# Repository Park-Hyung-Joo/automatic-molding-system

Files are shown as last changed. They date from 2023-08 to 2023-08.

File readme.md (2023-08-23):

--------------------------------------------
# Plastic Injection Molding Control System

## Abstract

This work was developed by the startup 'The Fourth Space', where senior Kim Seong-jun from the 17th generation of Barami is affiliated, as an outsourcing project for Barami's plastic injection molding machine control system.

The system is mainly divided into a heating bed (heater) that melts the plastic, a temperature sensor, and a solenoid valve that applies pressure to the melted plastic. Both the heater and the valve operate on 220VAC alternating current.

To control the 220VAC AC heater, a triac, a bidirectional switching device, was used. To control multiple triacs, each control signal is input to a 3-state buffer using a shift resistor, and the control signal is generated at the appropriate timing through a zero-detection circuit to turn the buffer on/off. This method allows for controlling the power of the AC heater. Additionally, the temperature of the AC heater is measured using a K-type temperature sensor, and by comparing it with the target temperature, the AC heater can be controlled within a range of 10 degrees of error through ON/OFF control. The solenoid valve also operates on 220VAC, so it is controlled in the same way using a triac.

--------------------------------------------------

## 220VAC Heater Control

### Triac
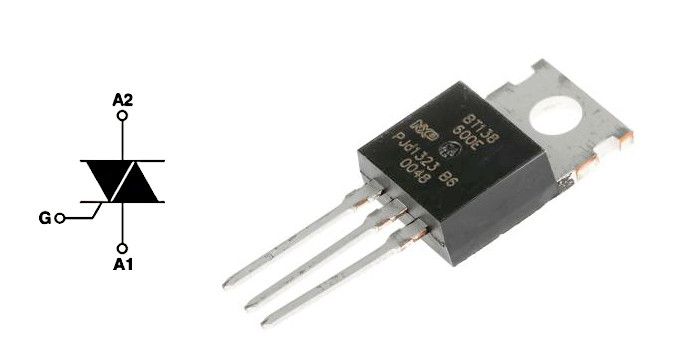
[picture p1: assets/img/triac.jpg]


A triac is a bidirectional switching device for high voltage and high current. When a pulse signal is given to the Gate, it shorts between A1 and A2 as long as the voltage value is above a certain level, and it disconnects again when the voltage drops below a threshold. The direction doesn't matter. In other words, by providing a pulse when the instantaneous voltage of the AC is 0, AC current can flow through the triac. This can be used to control the current flowing to the heater and valve.

## Triac control system

### Optocoupler Circuit

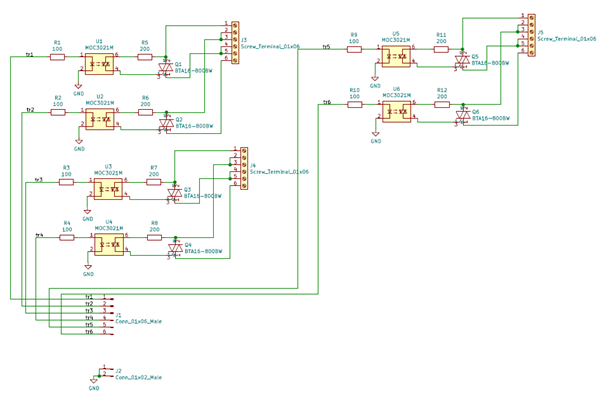
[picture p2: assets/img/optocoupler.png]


When pulses are provided to tr1~tr6 at the appropriate timing, AC current flows to the heaters connected to J3, J4, and J5. When the pulse supply is stopped, the current is cut off from the moment the AC instantaneous voltage becomes 0. The MOC3021(U1U6) device is an optocoupler, which separates the high current, high voltage AC circuit from the low voltage, low current DC circuit.

### Pulse Generator
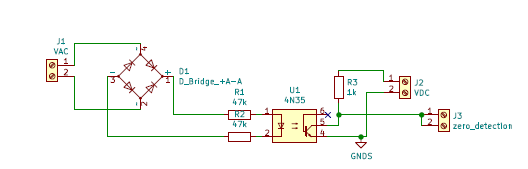
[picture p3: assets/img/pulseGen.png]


The circuit that generates the pulse produces a pulse at J3 the moment the AC voltage becomes 0. The detailed principle is as follows:

220VAC is rectified through bridge diodes and, through a resistor, provides the Photocoupler 4N35 with a rectified signal that has the same phase as 220VAC but at a lower voltage. When voltage is applied to the primary side of the 4N35, the secondary side's bjt operates, making the zero detection signal become 0. When the primary side voltage is 0, the bjt does not operate, and the zero detection voltage becomes VDC. Therefore, a pulse is generated the moment the voltage of 220VAC becomes 0.

This pulse is input into the 3-state buffer circuit.

### Tri-state Buffers
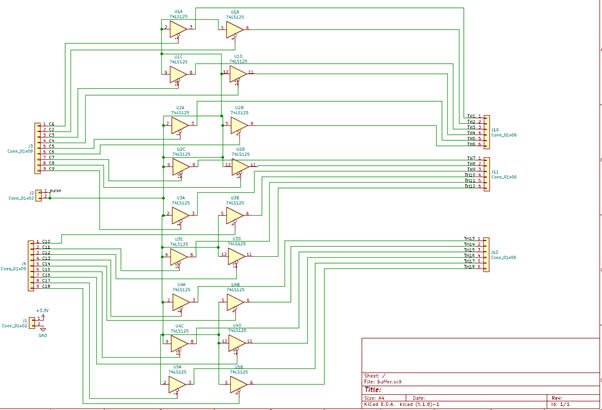
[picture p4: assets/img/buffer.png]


The tri-state buffer (buffer hereafter) circuit is divided into pulseIn, signal input, and pulseOut. When 0 is input to the signal input, the buffer passes the pulse, and when 1 is input, the pulse is blocked in the buffer. PulseOut is connected to tr1~tr6 of the above optocoupler circuit (there are a total of 3 optocoupler circuit boards). The triac is controlled by determining the signal value given to the buffer from the Arduino.

### Shift Registers
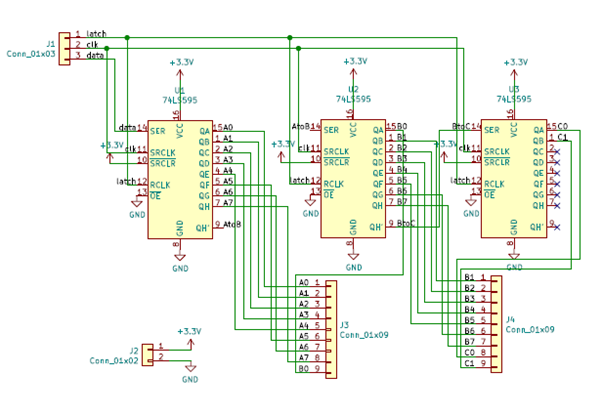
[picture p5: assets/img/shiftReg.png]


Directly inputting signals from the Arduino is unstable due to reasons like the insufficient number of Arduino pins and unstable signal current. Therefore, a method was chosen to store pre-determined signals in the shift register and connect the shift register output to the buffer signal end.

--------------------------------------------

## Temperature Measuring

To determine the current supplied to the heater, the temperature of the heating blocks must be measured. The temperature measurement circuit is composed of multiple temperature sensors and a decoder circuit to control them

### Temperature Sensers
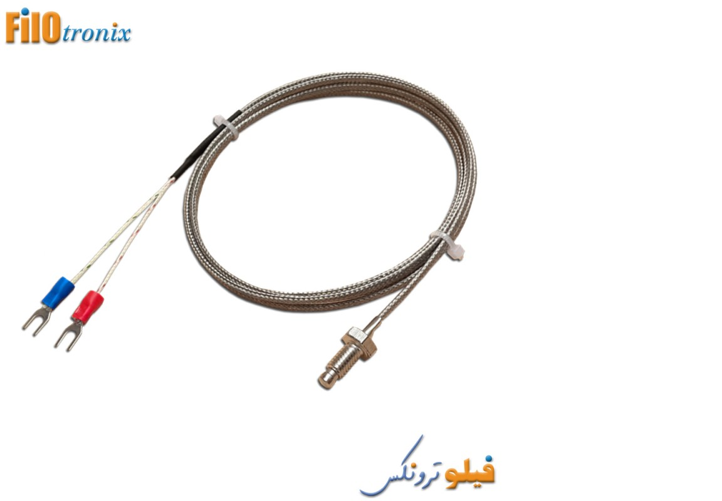
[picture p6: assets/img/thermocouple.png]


The advantage of the K-type temperature sensor is its wide usable temperature range. It's suitable for systems that need to operate at high temperatures, which is why it was used in this project.

### Temperature Senser Connection Bus
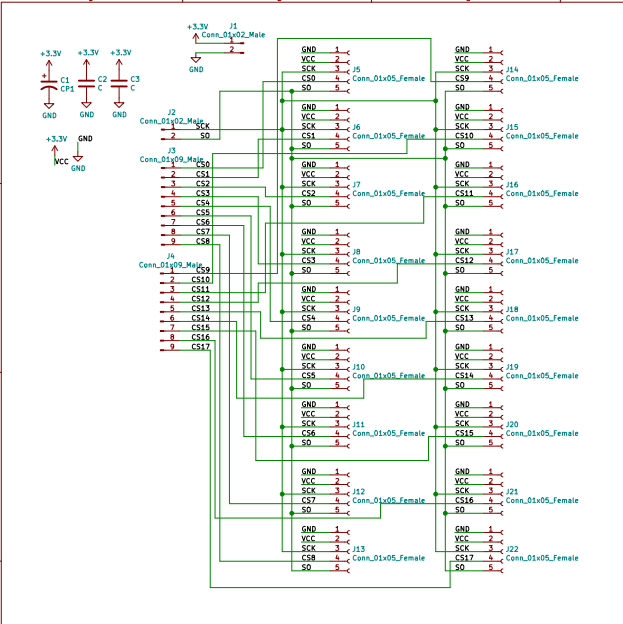
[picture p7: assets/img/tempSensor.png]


The temperature sensor communicates its measurements to the Arduino via SPI communication. SCK is the clock, SO is the data, and CS is the pin that determines the communication blockage.

### Decoders
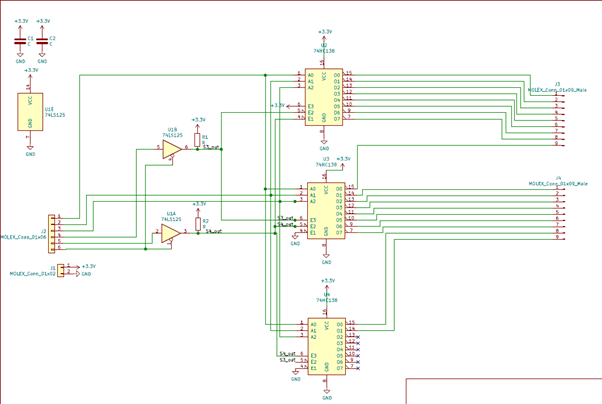
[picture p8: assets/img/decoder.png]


Since the Arduino can access only one temperature sensor at a time, only the selected temperature sensor should be connected to the Arduino, and the rest should be temporarily disconnected. The CS pin of the temperature sensor serves this function, and the values to be input into the CS pins are output through the decoder. The Arduino selects the temperature sensor to connect by inputting binary numbers to the decoder.

---------------------------------------------------------

## Solenoid Valve
<video src="./assets/img/valve.mp4" width="720px"></video>

A solenoid valve is applied to press the melted plastic. The control method is the same as the heater, using a triac. Since the same type of circuit is used, a detailed circuit description is omitted.

--------------------------------------------------------

## Raspberry Pi

While controlling the system with Arduino is sufficient, the client requested remote control functionality through a web application, so the Arduino was connected to the web via a Raspberry Pi.



--------------------------------------------------------

## Assembled Borads


This is how the circuit board looks when connected to the machine.

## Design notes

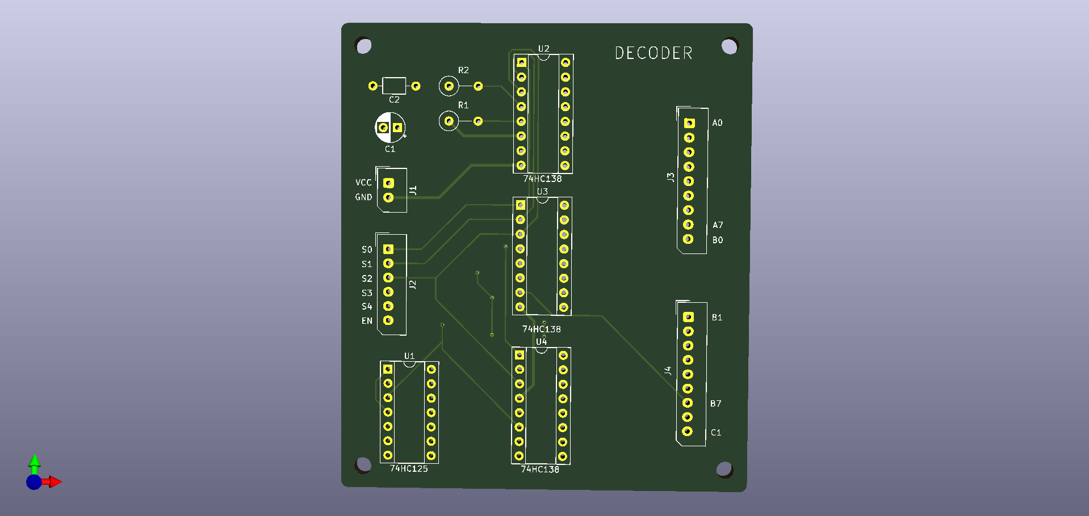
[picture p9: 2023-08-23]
hardware/decoder/decoder.png

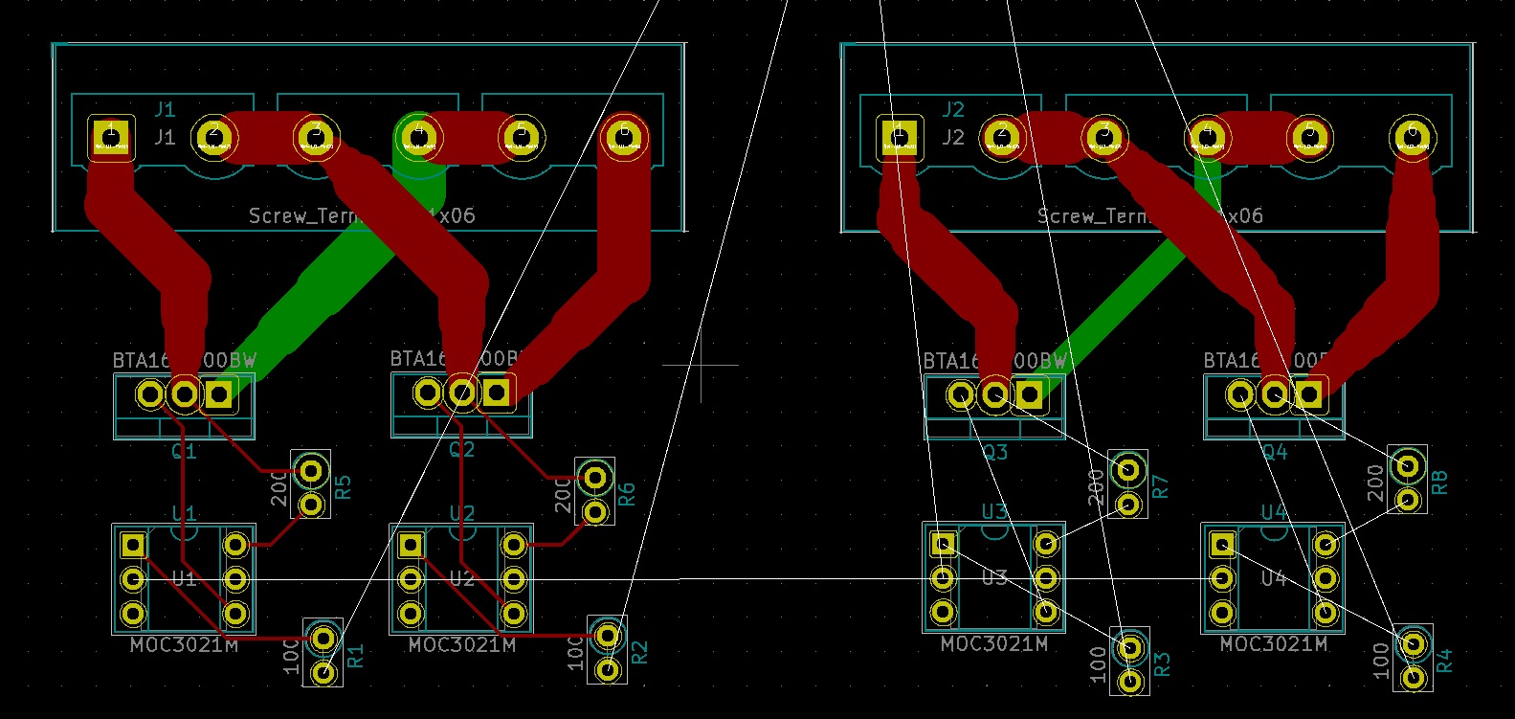
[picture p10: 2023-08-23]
hardware/triac_new/semi.jpg

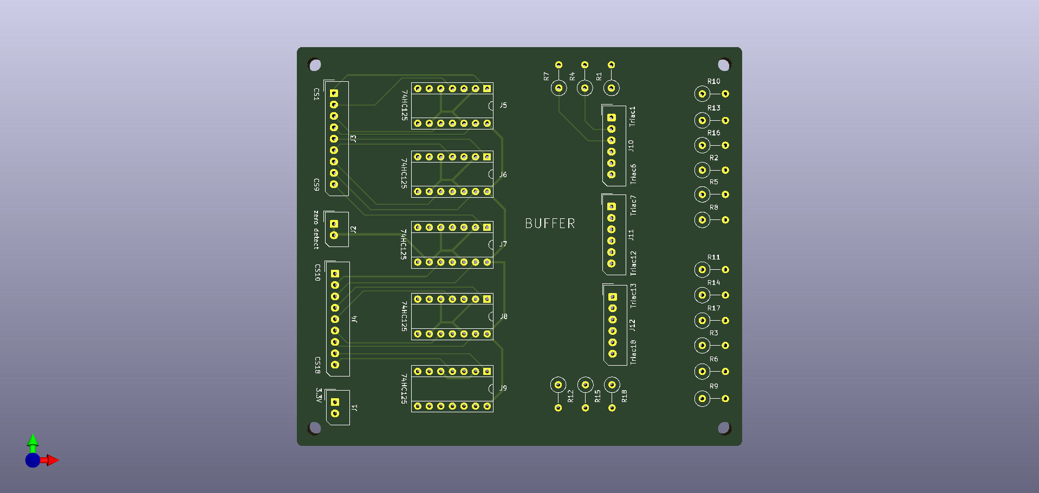
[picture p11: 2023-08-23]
hardware/buffer/buffer.png

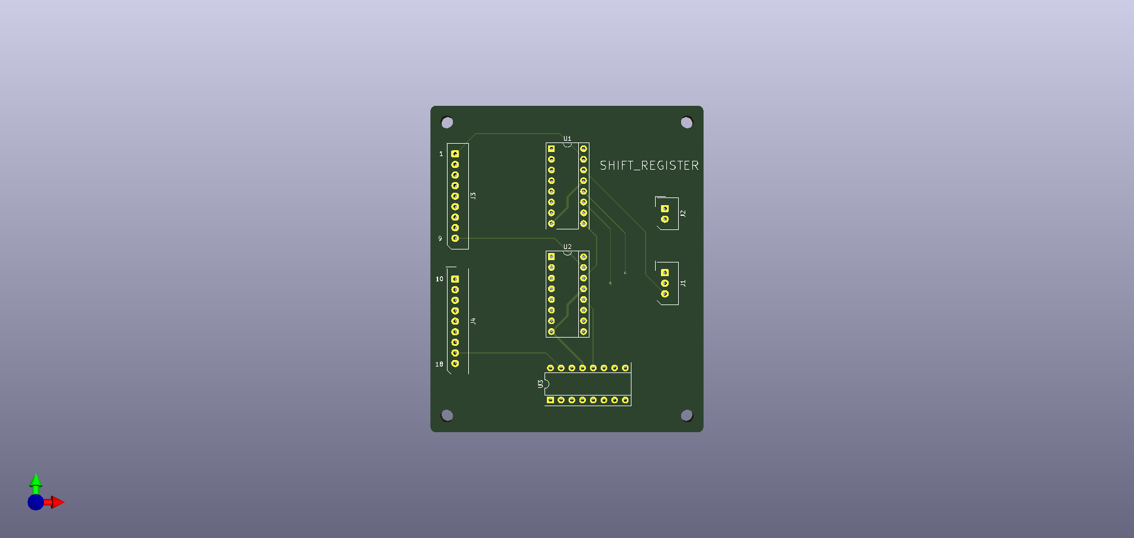
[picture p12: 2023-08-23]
hardware/shift_register/shift_register.png

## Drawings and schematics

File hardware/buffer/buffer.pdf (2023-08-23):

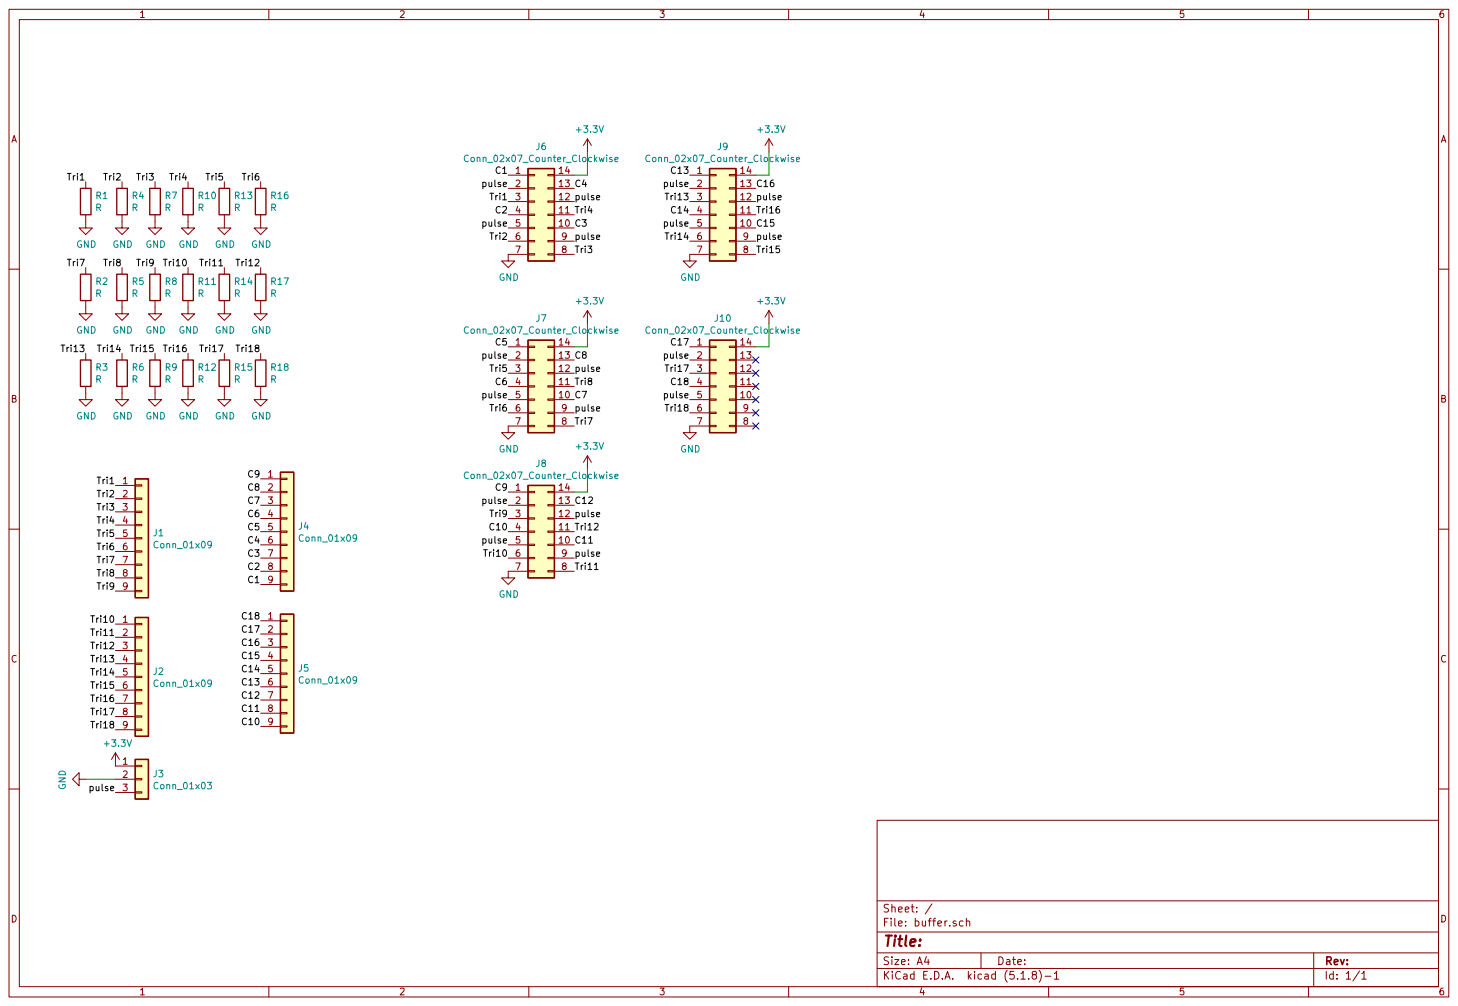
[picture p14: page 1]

Id: 1/1 Title: File: buffer.sch Sheet: /

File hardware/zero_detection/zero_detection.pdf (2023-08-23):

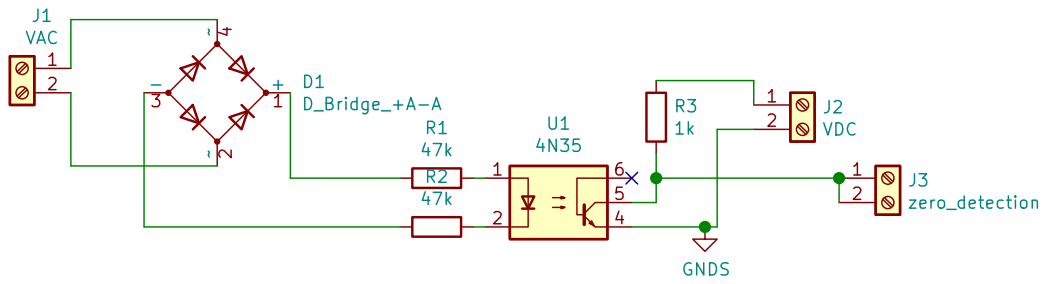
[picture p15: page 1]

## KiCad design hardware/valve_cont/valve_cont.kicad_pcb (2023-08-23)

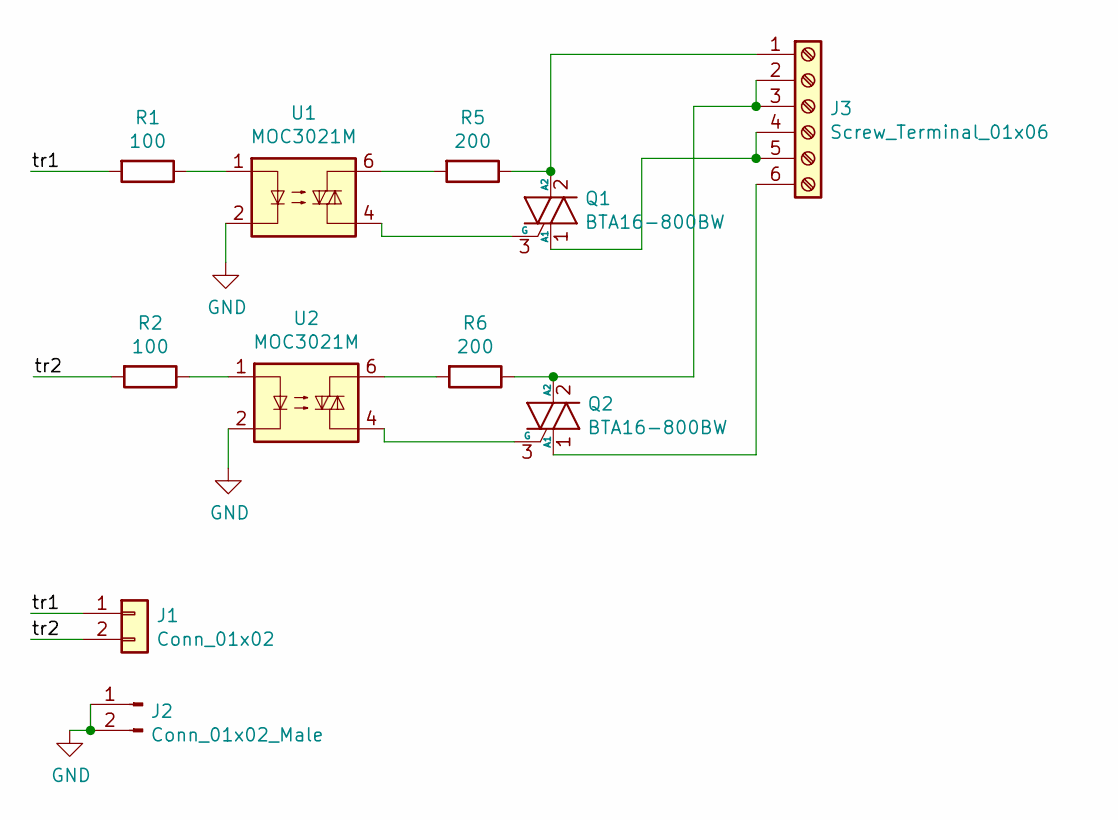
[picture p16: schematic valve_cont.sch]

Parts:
J1: Conn_01x02; Molex_SPOX_5267-02A_1x02_P2.50mm_Vertical
J2: Conn_01x02_Male; Molex_SPOX_5267-02A_1x02_P2.50mm_Vertical
J3: Screw_Terminal_01x06; BR_762K_6pin
Q1, Q2: BTA16-800BW; TO-220-3_Vertical
R1, R2: 100; R_Axial_DIN0207_L6.3mm_D2.5mm_P2.54mm_Vertical
R5, R6: 200; R_Axial_DIN0207_L6.3mm_D2.5mm_P2.54mm_Vertical
U1, U2: MOC3021M; DIP-6_W7.62mm_Socket

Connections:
/tr1: J1.1, R1.2
/tr2: J1.2, R2.2
GND: J2.1, J2.2, U1.2, U2.2
unnamed: J3.1, Q1.2 (A2), R5.1
unnamed: J3.2, J3.3, Q2.2 (A2), R6.1
unnamed: J3.4, J3.5, Q1.1 (A1)
unnamed: J3.6, Q2.1 (A1)
unnamed: Q1.3 (G), U1.4
unnamed: Q2.3 (G), U2.4
unnamed: R1.1, U1.1
unnamed: R2.1, U2.1
unnamed: R5.2, U1.6
unnamed: R6.2, U2.6

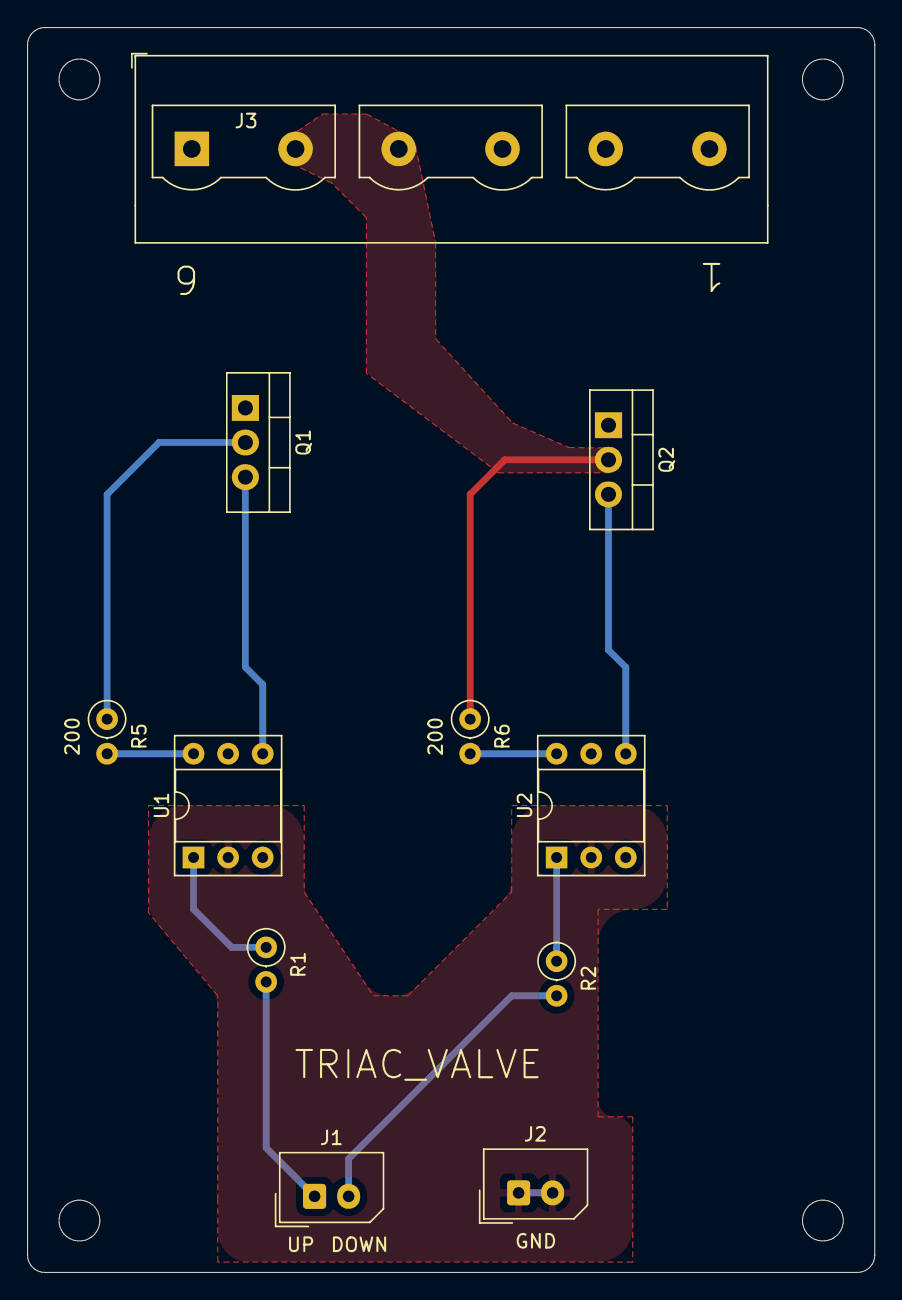
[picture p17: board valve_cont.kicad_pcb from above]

Board: 2 copper layers, 62.2 x 91.4 mm, 11 parts (0 on the bottom side), 13 nets.

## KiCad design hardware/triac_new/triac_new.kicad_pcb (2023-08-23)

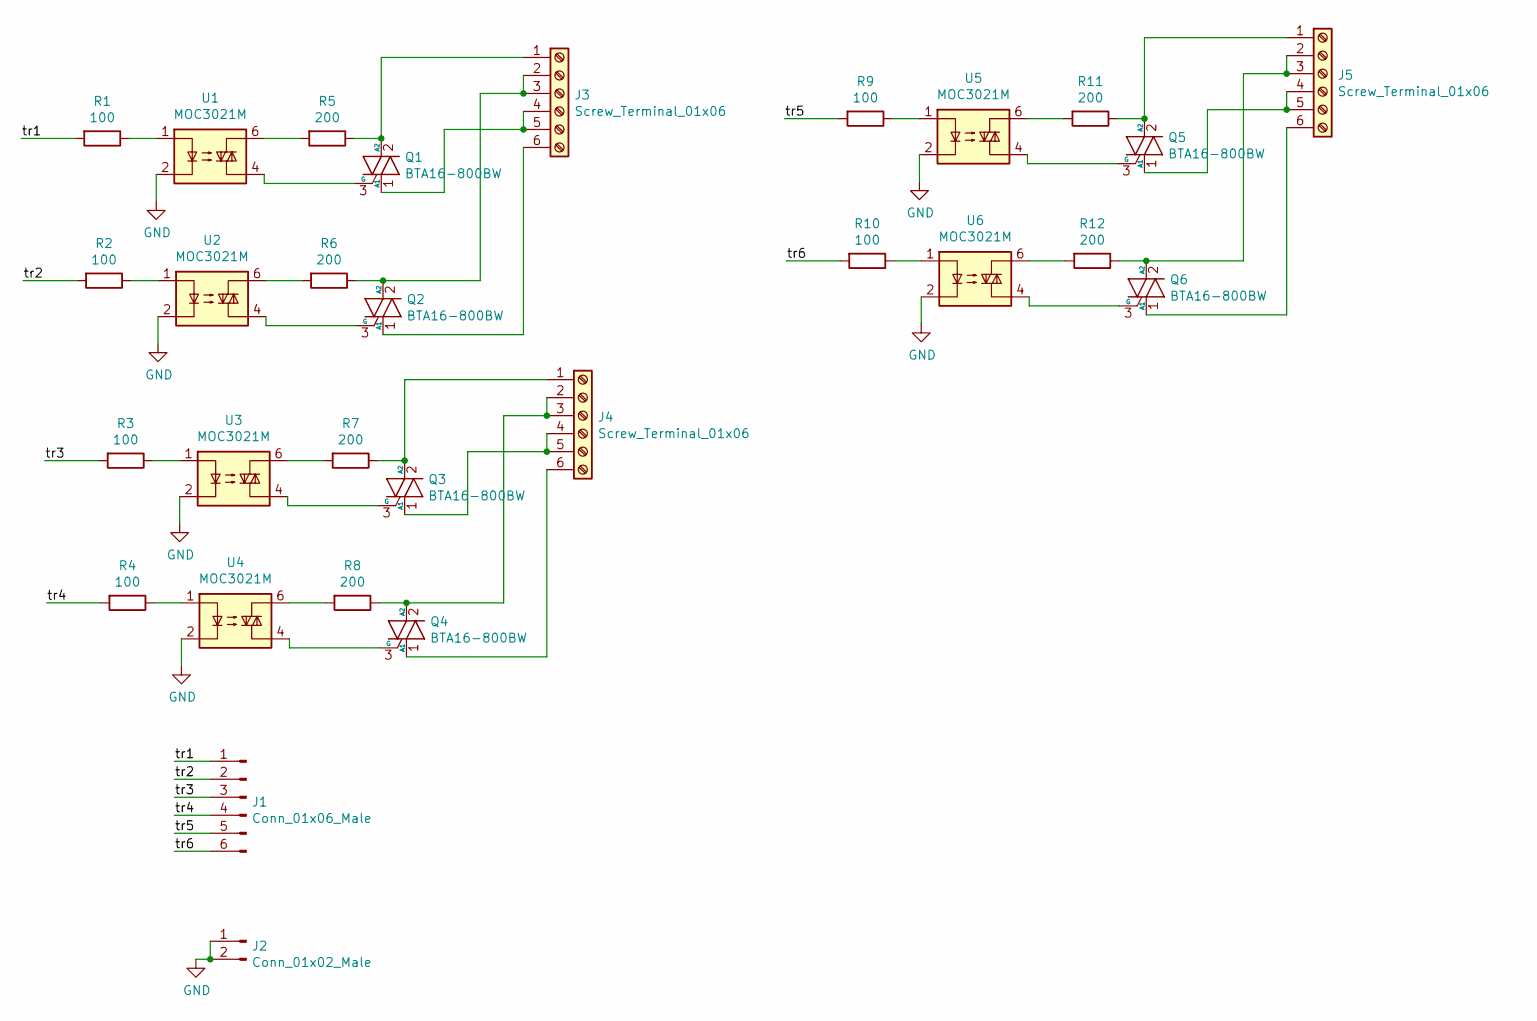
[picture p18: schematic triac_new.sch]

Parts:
J1: Conn_01x06_Male; Molex_SPOX_5267-06A_1x06_P2.50mm_Vertical
J2: Conn_01x02_Male; Molex_SPOX_5267-02A_1x02_P2.50mm_Vertical
J3, J4, J5: Screw_Terminal_01x06; BR_762K_6pin
Q1, Q2, Q3, Q4, Q5, Q6: BTA16-800BW; TO-220-3_Vertical
R1, R2, R3, R4, R9, R10: 100; R_Axial_DIN0207_L6.3mm_D2.5mm_P2.54mm_Vertical
R5, R6, R7, R8, R11, R12: 200; R_Axial_DIN0207_L6.3mm_D2.5mm_P2.54mm_Vertical
U1, U2, U3, U4, U5, U6: MOC3021M; DIP-6_W7.62mm_Socket

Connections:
/tr1: J1.1, R1.2
/tr2: J1.2, R2.2
/tr3: J1.3, R3.2
/tr4: J1.4, R4.2
/tr5: J1.5, R9.2
/tr6: J1.6, R10.2
GND: J2.1, J2.2, U1.2, U2.2, U3.2, U4.2, U5.2, U6.2
unnamed: J3.1, Q1.2 (A2), R5.1
unnamed: J3.2, J3.3, Q2.2 (A2), R6.1
unnamed: J3.4, J3.5, Q1.1 (A1)
unnamed: J3.6, Q2.1 (A1)
unnamed: J4.1, Q3.2 (A2), R7.1
unnamed: J4.2, J4.3, Q4.2 (A2), R8.1
unnamed: J4.4, J4.5, Q3.1 (A1)
unnamed: J4.6, Q4.1 (A1)
unnamed: J5.1, Q5.2 (A2), R11.1
unnamed: J5.2, J5.3, Q6.2 (A2), R12.1
unnamed: J5.4, J5.5, Q5.1 (A1)
unnamed: J5.6, Q6.1 (A1)
unnamed: Q1.3 (G), U1.4
unnamed: Q2.3 (G), U2.4
unnamed: Q3.3 (G), U3.4
unnamed: Q4.3 (G), U4.4
unnamed: Q5.3 (G), U5.4
unnamed: Q6.3 (G), U6.4
unnamed: R1.1, U1.1
unnamed: R2.1, U2.1
unnamed: R3.1, U3.1
unnamed: R4.1, U4.1
unnamed: R5.2, U1.6
unnamed: R6.2, U2.6
unnamed: R7.2, U3.6
unnamed: R8.2, U4.6
unnamed: R9.1, U5.1
unnamed: R10.1, U6.1
unnamed: R11.2, U5.6
unnamed: R12.2, U6.6

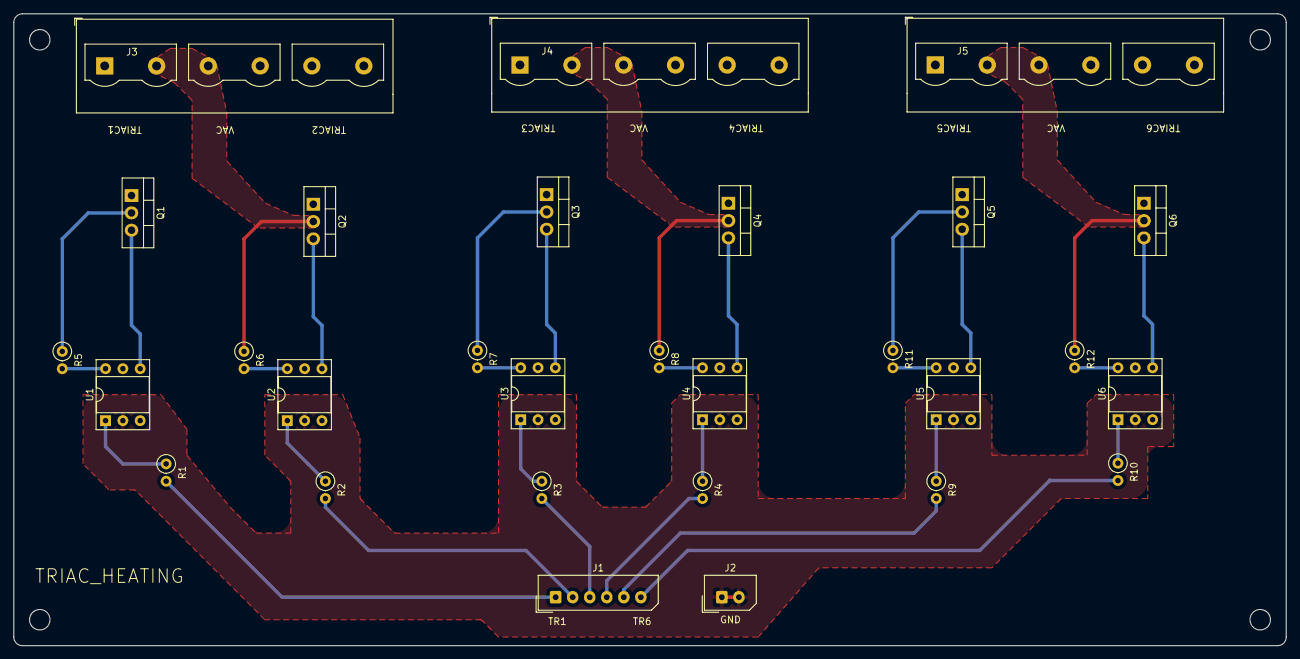
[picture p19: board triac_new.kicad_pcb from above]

Board: 2 copper layers, 186.7 x 92.7 mm, 29 parts (0 on the bottom side), 37 nets.

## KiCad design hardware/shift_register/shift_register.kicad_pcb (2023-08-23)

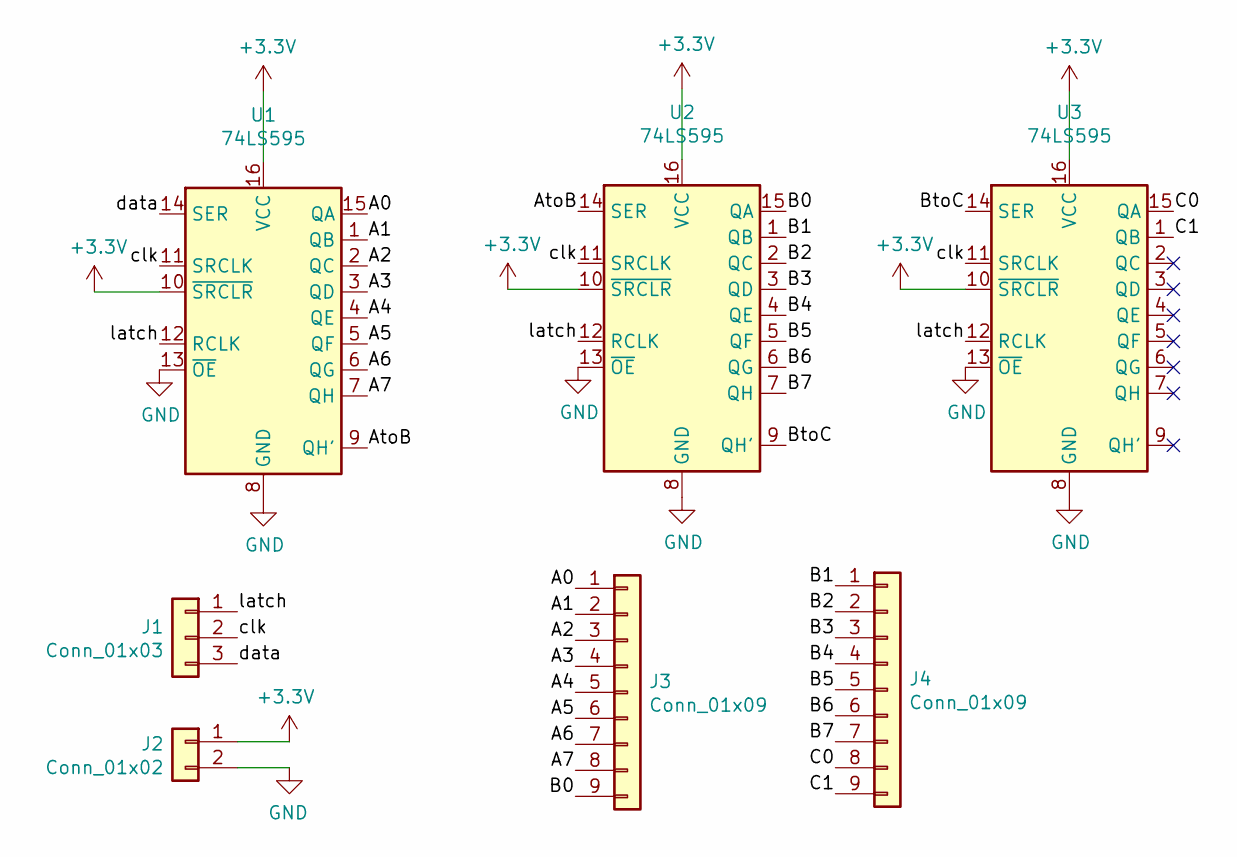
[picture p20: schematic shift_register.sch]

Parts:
J1: Conn_01x03; Molex_SPOX_5267-03A_1x03_P2.50mm_Vertical
J2: Conn_01x02; Molex_SPOX_5267-02A_1x02_P2.50mm_Vertical
J3, J4: Conn_01x09; Molex_SPOX_5267-09A_1x09_P2.50mm_Vertical
U1, U2, U3: 74LS595; DIP-16_W7.62mm_Socket

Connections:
+3V3: J2.1, U1.10 (~SRCLR), U1.16 (VCC), U2.10 (~SRCLR), U2.16 (VCC), U3.10 (~SRCLR), U3.16 (VCC)
/A0: J3.1, U1.15 (QA)
/A1: J3.2, U1.1 (QB)
/A2: J3.3, U1.2 (QC)
/A3: J3.4, U1.3 (QD)
/A4: J3.5, U1.4 (QE)
/A5: J3.6, U1.5 (QF)
/A6: J3.7, U1.6 (QG)
/A7: J3.8, U1.7 (QH)
/AtoB: U1.9 (QH'), U2.14 (SER)
/B0: J3.9, U2.15 (QA)
/B1: J4.1, U2.1 (QB)
/B2: J4.2, U2.2 (QC)
/B3: J4.3, U2.3 (QD)
/B4: J4.4, U2.4 (QE)
/B5: J4.5, U2.5 (QF)
/B6: J4.6, U2.6 (QG)
/B7: J4.7, U2.7 (QH)
/BtoC: U2.9 (QH'), U3.14 (SER)
/C0: J4.8, U3.15 (QA)
/C1: J4.9, U3.1 (QB)
/clk: J1.2, U1.11 (SRCLK), U2.11 (SRCLK), U3.11 (SRCLK)
/data: J1.3, U1.14 (SER)
/latch: J1.1, U1.12 (RCLK), U2.12 (RCLK), U3.12 (RCLK)
GND: J2.2, U1.8 (GND), U1.13 (~OE), U2.8 (GND), U2.13 (~OE), U3.8 (GND), U3.13 (~OE)

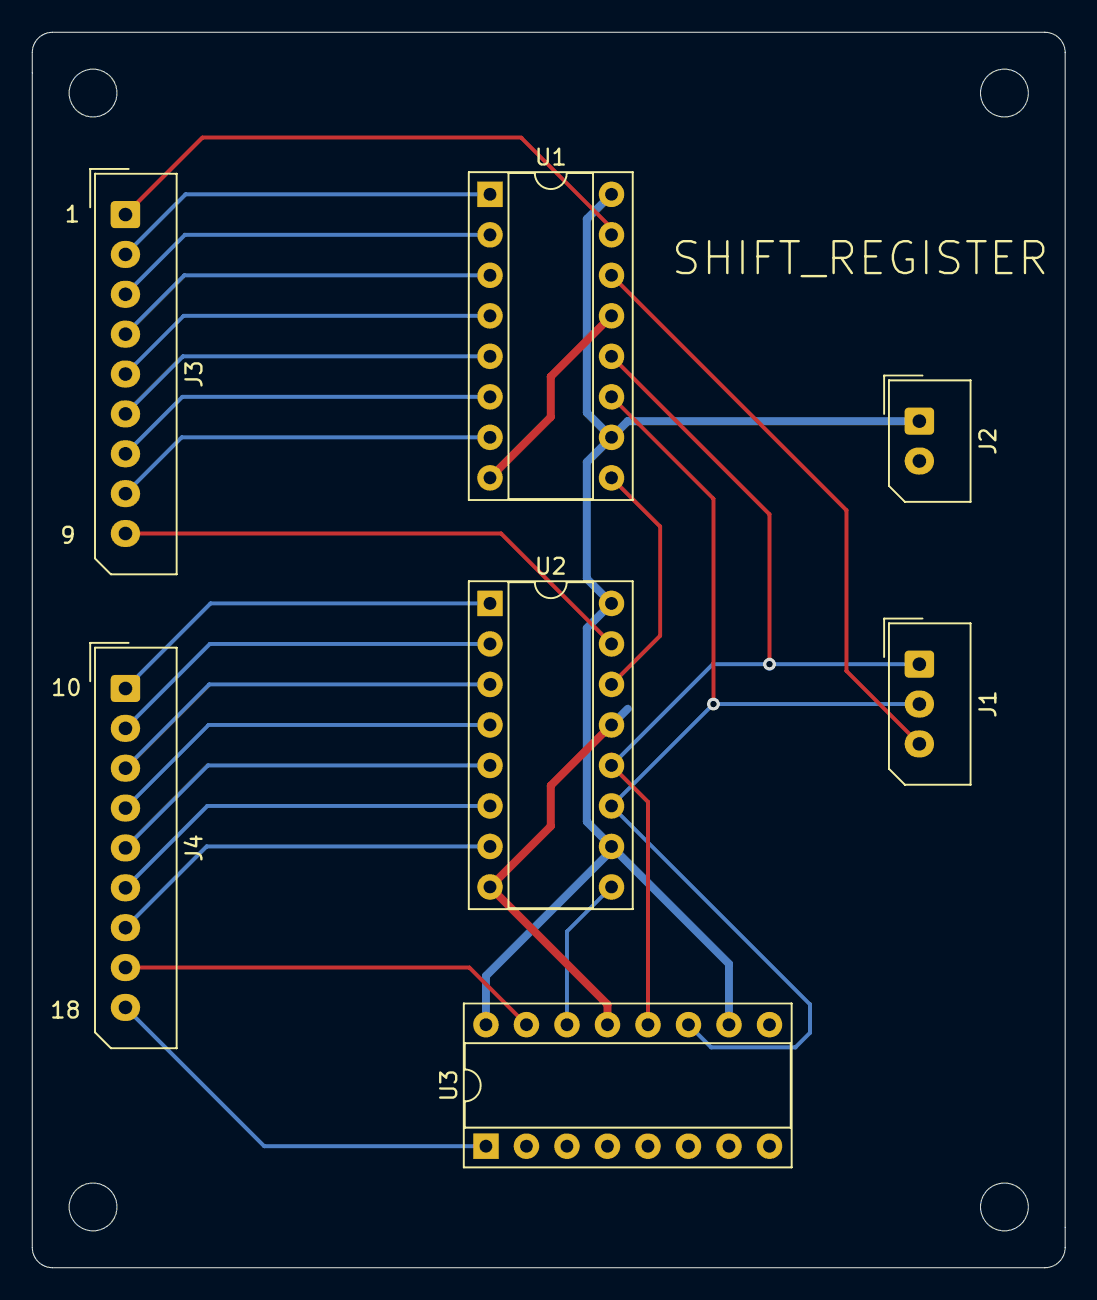
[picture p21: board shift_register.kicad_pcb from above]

Board: 2 copper layers, 64.8 x 77.5 mm, 7 parts (0 on the bottom side), 25 nets.

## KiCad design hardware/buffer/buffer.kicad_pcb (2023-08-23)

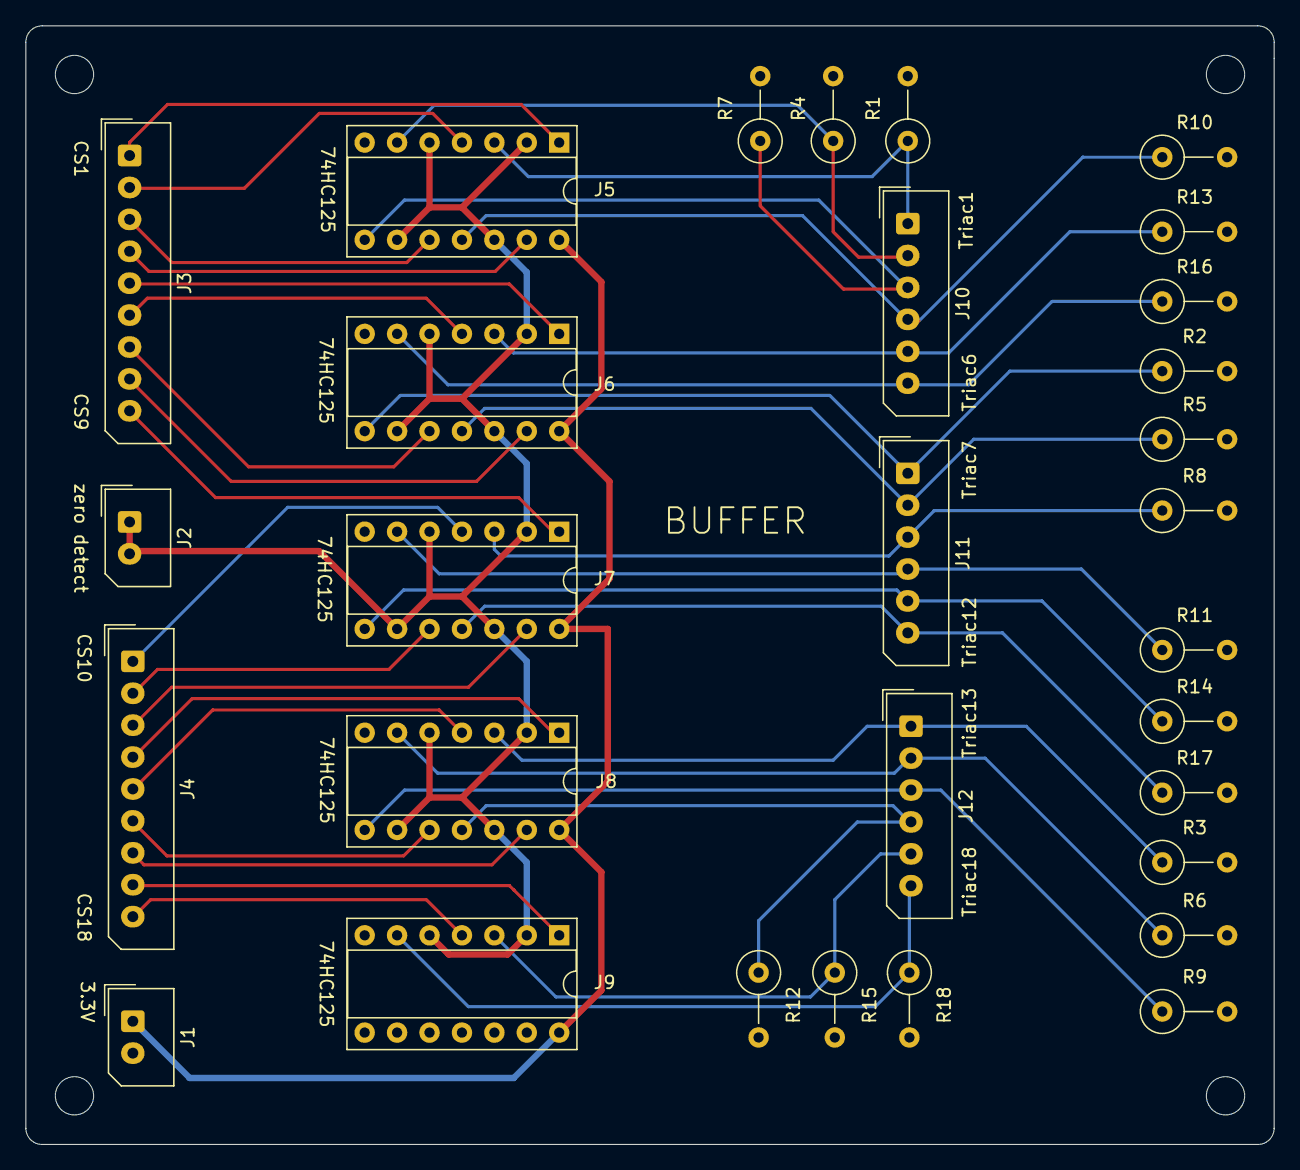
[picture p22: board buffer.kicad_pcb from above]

Board: 2 copper layers, 97.8 x 87.6 mm, 30 parts (0 on the bottom side), 39 nets.

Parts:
J1, J2: Conn_01x02; Molex_SPOX_5267-02A_1x02_P2.50mm_Vertical
J3, J4: Conn_01x09; Molex_SPOX_5267-09A_1x09_P2.50mm_Vertical
J5, J6, J7, J8, J9: Conn_02x07_Counter_Clockwise; DIP-14_W7.62mm_Socket
J10, J11, J12: Conn_01x06; Molex_SPOX_5267-06A_1x06_P2.50mm_Vertical
R1, R2, R3, R4, R5, R6, R7, R8, R9, R10, R11, R12, R13, R14, R15, R16, R17, R18: R; R_Axial_DIN0309_L9.0mm_D3.2mm_P5.08mm_Vertical

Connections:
+3V3: J1.1, J5.14, J6.14, J7.14, J8.14, J9.14
/C1: J3.1, J5.1
/C2: J3.2, J5.4
/C3: J3.3, J5.10
/C4: J3.4, J5.13
/C5: J3.5, J6.1
/C6: J3.6, J6.4
/C7: J3.7, J6.10
/C8: J3.8, J6.13
/C9: J3.9, J7.1
/C10: J4.1, J7.4
/C11: J4.2, J7.10
/C12: J4.3, J7.13
/C13: J4.4, J8.1
/C14: J4.5, J8.4
/C15: J4.6, J8.10
/C16: J4.7, J8.13
/C17: J4.8, J9.1
/C18: J4.9, J9.4
/Tri1: J5.3, J10.1, R1.1
/Tri2: J5.6, J10.2, R4.1
/Tri3: J5.8, J10.3, R7.1
/Tri4: J5.11, J10.4, R10.1
/Tri5: J6.3, J10.5, R13.1
/Tri6: J6.6, J10.6, R16.1
/Tri7: J6.8, J11.1, R2.1
/Tri8: J6.11, J11.2, R5.1
/Tri9: J7.3, J11.3, R8.1
/Tri10: J7.6, J11.4, R11.1
/Tri11: J7.8, J11.5, R14.1
/Tri12: J7.11, J11.6, R17.1
/Tri13: J8.3, J12.1, R3.1
/Tri14: J8.6, J12.2, R6.1
/Tri15: J8.8, J12.3, R9.1
/Tri16: J8.11, J12.4, R12.1
/Tri17: J9.3, J12.5, R15.1
/Tri18: J9.6, J12.6, R18.1
/pulse: J2.1, J2.2, J5.2, J5.5, J5.9, J5.12, J6.2, J6.5, J6.9, J6.12, J7.2, J7.5, J7.9, J7.12, J8.2, J8.5, J8.9, J8.12, J9.2, J9.5
GND: J1.2, J5.7, J6.7, J7.7, J8.7, J9.7, R1.2, R2.2, R3.2, R4.2, R5.2, R6.2, R7.2, R8.2, R9.2, R10.2, R11.2, R12.2, R13.2, R14.2, R15.2, R16.2, R17.2, R18.2

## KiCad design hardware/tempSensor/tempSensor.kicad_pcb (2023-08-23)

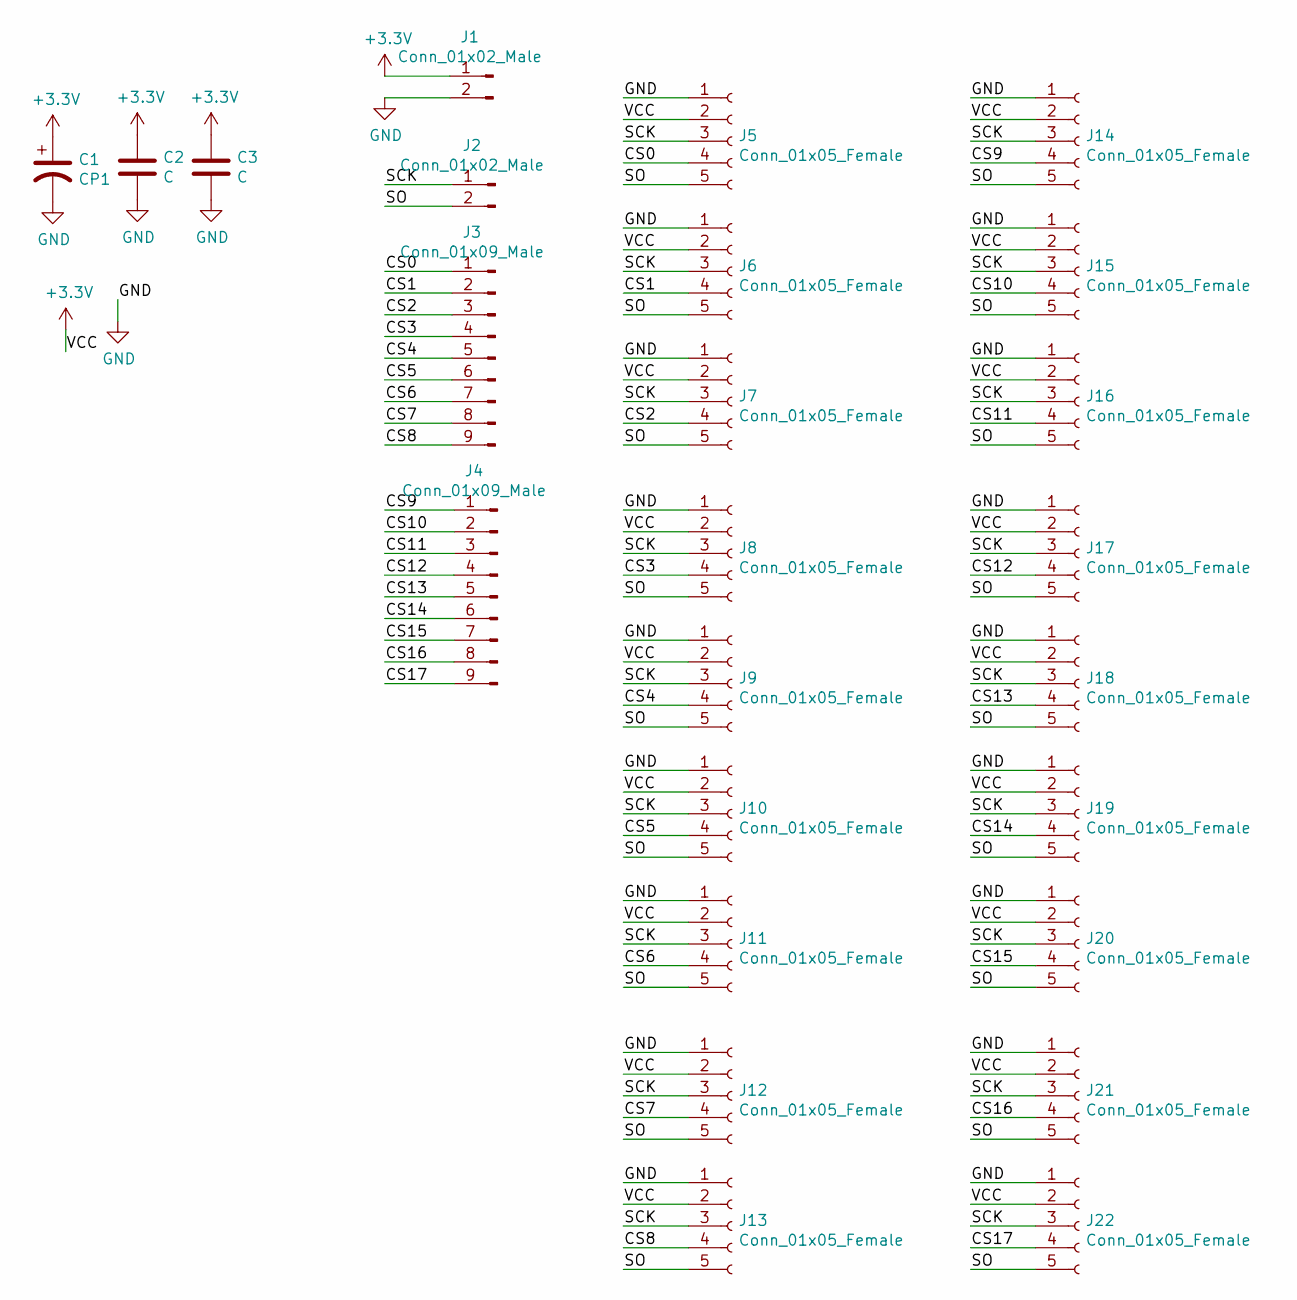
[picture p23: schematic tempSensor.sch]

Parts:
C1: CP1; CP_Radial_D8.0mm_P5.00mm
C2, C3: C; C_Axial_L3.8mm_D2.6mm_P7.50mm_Horizontal
J1, J2: Conn_01x02_Male; Molex_SPOX_5267-02A_1x02_P2.50mm_Vertical
J3, J4: Conn_01x09_Male; Molex_SPOX_5267-09A_1x09_P2.50mm_Vertical
J5, J6, J7, J8, J9, J10, J11, J12, J13, J14, J15, J16, J17, J18, J19, J20, J21, J22: Conn_01x05_Female; PinSocket_1x05_P2.54mm_Vertical

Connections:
+3V3: C1.1, C2.1, C3.1, J1.1, J5.2, J6.2, J7.2, J8.2, J9.2, J10.2, J11.2, J12.2, J13.2, J14.2, J15.2, J16.2, J17.2, J18.2, J19.2, J20.2, J21.2, J22.2
/CS0: J3.1, J5.4
/CS1: J3.2, J6.4
/CS2: J3.3, J7.4
/CS3: J3.4, J8.4
/CS4: J3.5, J9.4
/CS5: J3.6, J10.4
/CS6: J3.7, J11.4
/CS7: J3.8, J12.4
/CS8: J3.9, J13.4
/CS9: J4.1, J14.4
/CS10: J4.2, J15.4
/CS11: J4.3, J16.4
/CS12: J4.4, J17.4
/CS13: J4.5, J18.4
/CS14: J4.6, J19.4
/CS15: J4.7, J20.4
/CS16: J4.8, J21.4
/CS17: J4.9, J22.4
/SCK: J2.1, J5.3, J6.3, J7.3, J8.3, J9.3, J10.3, J11.3, J12.3, J13.3, J14.3, J15.3, J16.3, J17.3, J18.3, J19.3, J20.3, J21.3, J22.3
/SO: J2.2, J5.5, J6.5, J7.5, J8.5, J9.5, J10.5, J11.5, J12.5, J13.5, J14.5, J15.5, J16.5, J17.5, J18.5, J19.5, J20.5, J21.5, J22.5
GND: C1.2, C2.2, C3.2, J1.2, J5.1, J6.1, J7.1, J8.1, J9.1, J10.1, J11.1, J12.1, J13.1, J14.1, J15.1, J16.1, J17.1, J18.1, J19.1, J20.1, J21.1, J22.1

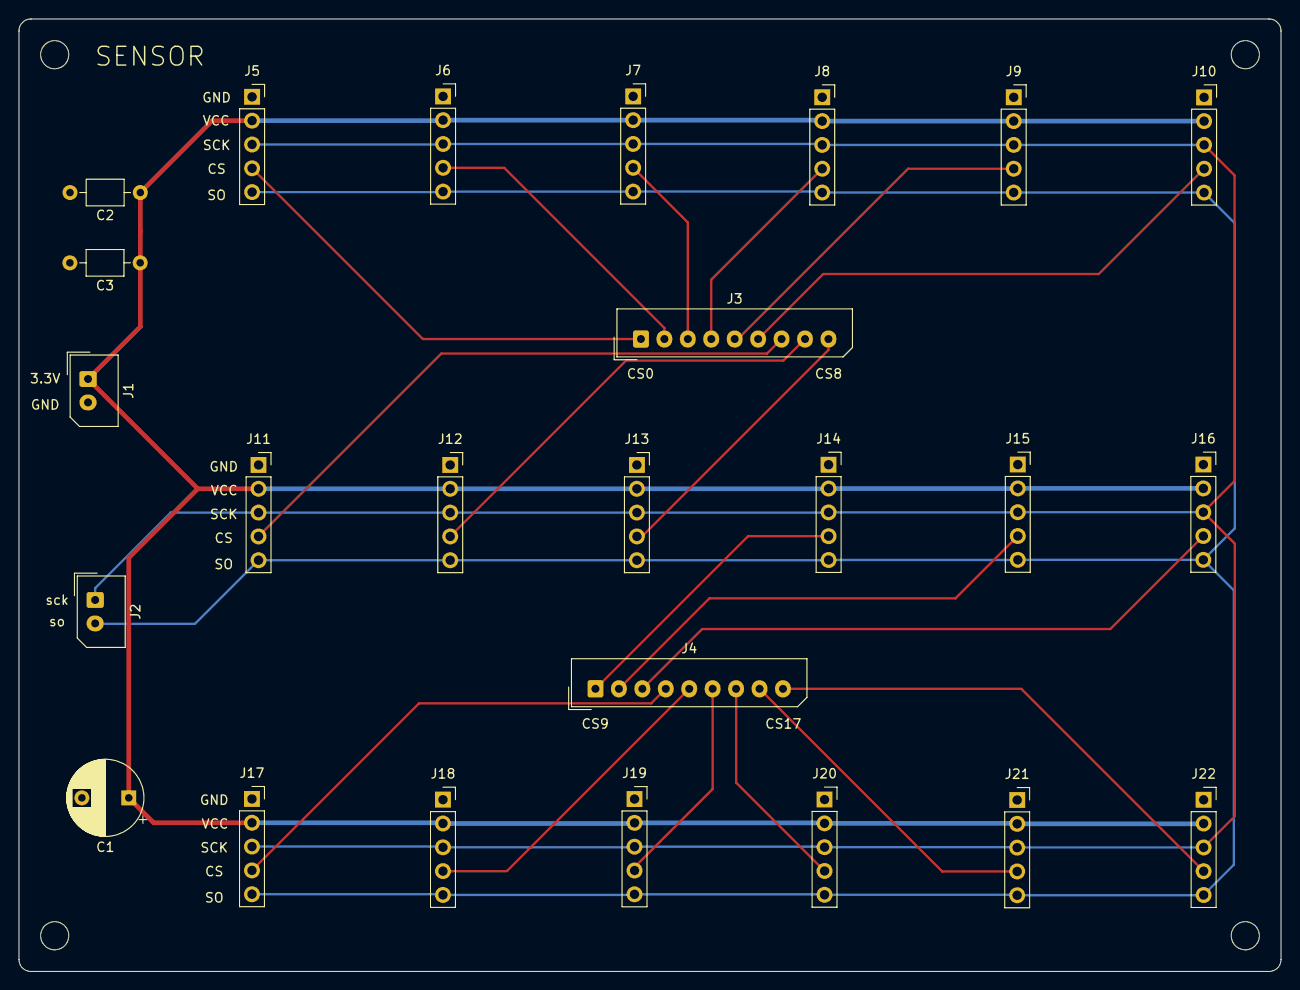
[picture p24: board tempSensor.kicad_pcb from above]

Board: 2 copper layers, 134.6 x 101.6 mm, 25 parts (0 on the bottom side), 22 nets.

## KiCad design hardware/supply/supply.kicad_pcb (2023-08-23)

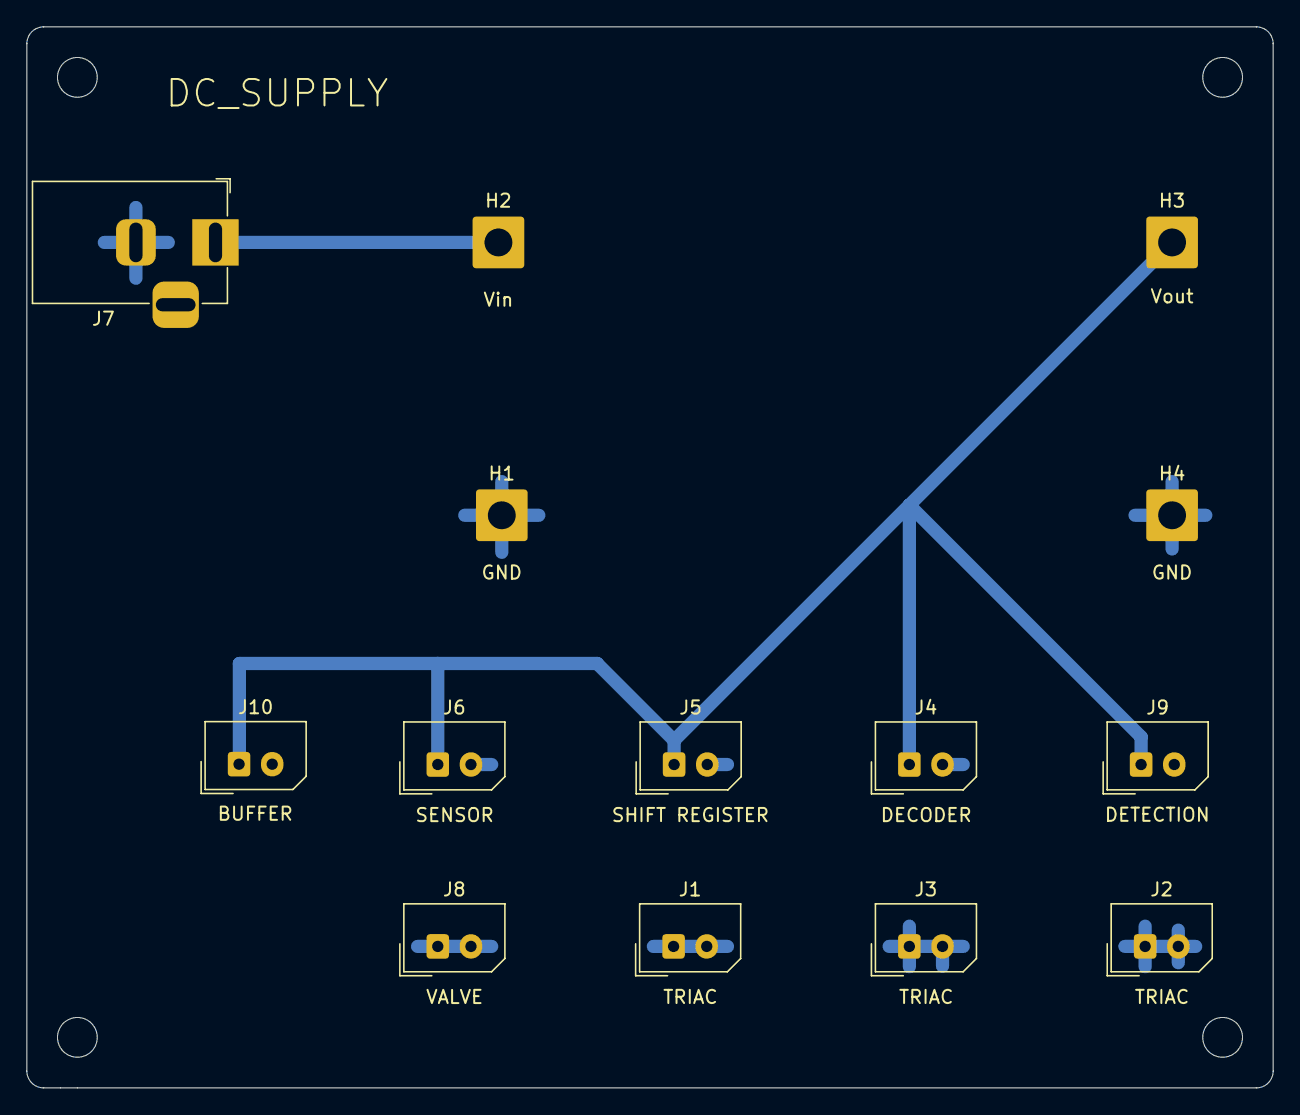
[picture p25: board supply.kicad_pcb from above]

Board: 2 copper layers, 94.0 x 80.0 mm, 14 parts (0 on the bottom side), 3 nets.

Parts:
H1, H2, H3, H4: MountingHole_Pad; SolderWire-1.5sqmm_1x01_D1.7mm_OD3.9mm
J1, J2, J3, J4, J5, J6, J8, J9, J10: Conn_01x02_Male; Molex_SPOX_5267-02A_1x02_P2.50mm_Vertical
J7: Barrel_Jack_Switch; BarrelJack_Horizontal

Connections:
+3V3: H3.1, J4.1, J5.1, J6.1, J9.1, J10.1
+12V: H2.1, J7.1
GND: H1.1, H4.1, J1.1, J1.2, J2.1, J2.2, J3.1, J3.2, J4.2, J5.2, J6.2, J7.2, J8.1, J8.2, J9.2, J10.2

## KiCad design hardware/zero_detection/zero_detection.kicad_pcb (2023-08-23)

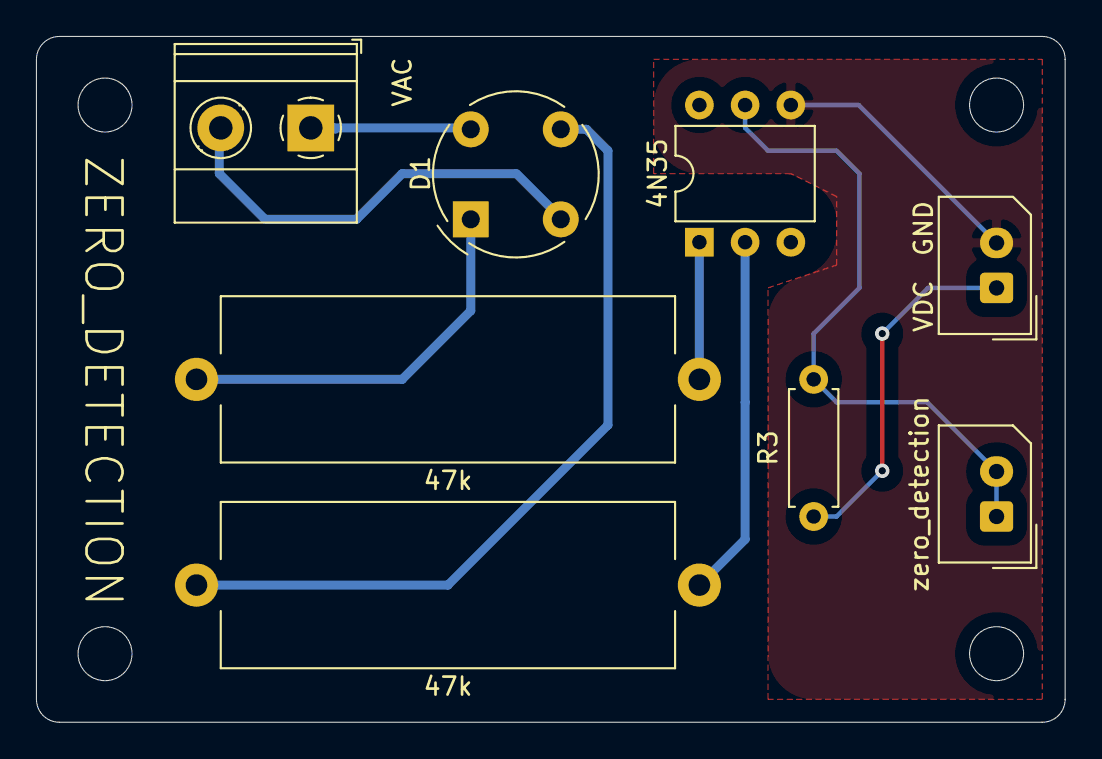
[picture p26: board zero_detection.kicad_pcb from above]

Board: 2 copper layers, 57.2 x 38.1 mm, 8 parts (0 on the bottom side), 9 nets.

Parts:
4N35: 4N35; DIP-6_W7.62mm
47k, 47k#2: 47k; R_Axial_Power_L25.0mm_W9.0mm_P27.94mm
D1: D_Bridge_+A-A; Diode_Bridge_Round_D9.0mm
R3: 1k; R_Axial_DIN0207_L6.3mm_D2.5mm_P7.62mm_Horizontal
VAC: VAC; TerminalBlock_Phoenix_MKDS-1,5-2_1x02_P5.00mm_Horizontal
VDC: VDC; Molex_SPOX_5267-02A_1x02_P2.50mm_Vertical
zero_detection: zero_detection; Molex_SPOX_5267-02A_1x02_P2.50mm_Vertical

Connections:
GNDS: 4N35.4, VDC.2
unnamed: 47k#2.2, D1.1
unnamed: D1.2, VAC.2
unnamed: 47k.2, D1.3
unnamed: D1.4, VAC.1
unnamed: R3.1, VDC.1
unnamed: 4N35.5, R3.2, zero_detection.1, zero_detection.2
unnamed: 4N35.1, 47k#2.1
unnamed: 4N35.2, 47k.1

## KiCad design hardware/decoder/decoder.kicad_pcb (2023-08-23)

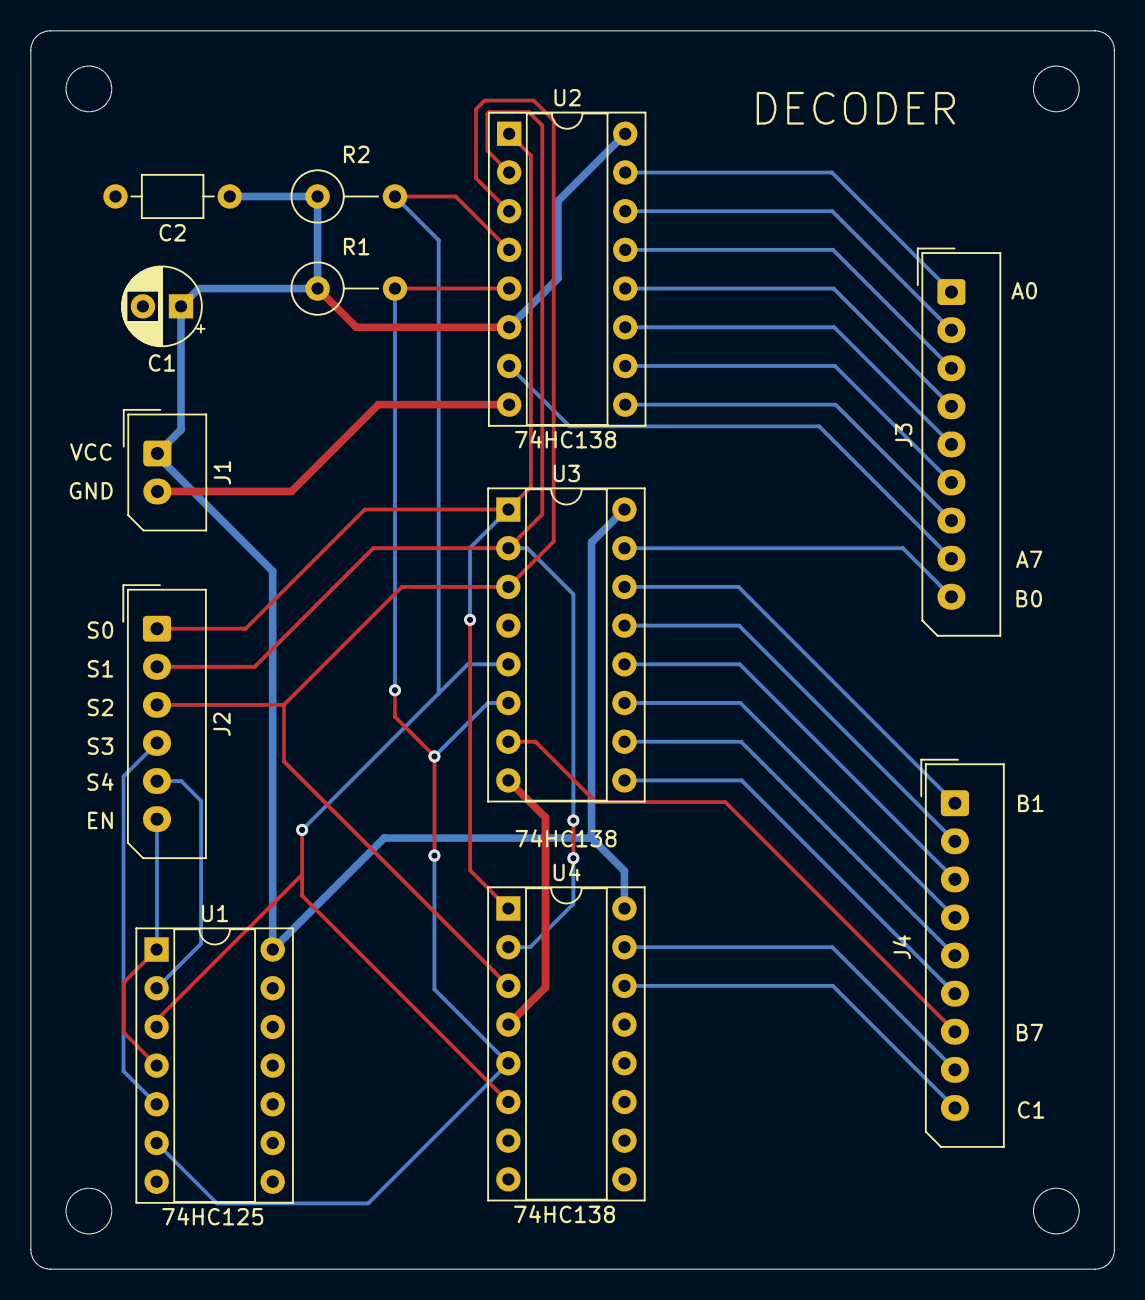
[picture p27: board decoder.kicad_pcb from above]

Board: 2 copper layers, 71.1 x 81.3 mm, 12 parts (0 on the bottom side), 28 nets.

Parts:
C1: C; CP_Radial_D5.0mm_P2.50mm
C2: C; C_Axial_L3.8mm_D2.6mm_P7.50mm_Horizontal
J1: Conn_01x02; Molex_SPOX_5267-02A_1x02_P2.50mm_Vertical
J2: Conn_01x06; Molex_SPOX_5267-06A_1x06_P2.50mm_Vertical
J3, J4: Conn_01x09_Male; Molex_SPOX_5267-09A_1x09_P2.50mm_Vertical
R1, R2: R; R_Axial_DIN0309_L9.0mm_D3.2mm_P5.08mm_Vertical
U1: 74LS125; DIP-14_W7.62mm_Socket
U2, U3, U4: 74LS138; DIP-16_W7.62mm_Socket

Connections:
+3V3: C1.1, C2.1, J1.1, R1.1, R2.1, U1.14, U2.6, U2.16, U3.16, U4.16
/S3_out: R1.2, U1.6, U2.5, U3.6, U4.5
/S4_out: R2.2, U1.3, U2.4, U3.5, U4.6
A0: J3.1, U2.15
A1: J3.2, U2.14
A2: J3.3, U2.13
A3: J3.4, U2.12
A4: J3.5, U2.11
A5: J3.6, U2.10
A6: J3.7, U2.9
A7: J3.8, U2.7
B0: J3.9, U3.15
B1: J4.1, U3.14
B2: J4.2, U3.13
B3: J4.3, U3.12
B4: J4.4, U3.11
B5: J4.5, U3.10
B6: J4.6, U3.9
B7: J4.7, U3.7
C0: J4.8, U4.15
C1: J4.9, U4.14
GND: C1.2, C2.2, J1.2, U1.7, U2.8, U3.4, U3.8, U4.4, U4.8
ON: J2.6, U1.1, U1.4
S0: J2.1, U2.1, U3.1, U4.1
S1: J2.2, U2.2, U3.2, U4.2
S2: J2.3, U2.3, U3.3, U4.3
S3: J2.4, U1.5
S4: J2.5, U1.2

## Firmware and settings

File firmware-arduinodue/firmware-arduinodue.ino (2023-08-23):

// include Arduino standard library
#include <SPI.h>
#include <Wire.h>
#include <stdio.h>
// include FreeRTOS
#include "src/FreeRTOS_ARM/FreeRTOS_ARM.h"

// pin setting constant
#define PIN_TEMPSENSOR_DECODER_ENABLE 23
#define PIN_TRIAC_SHIFTRESISTOR_DATA 41
#define PIN_TRIAC_SHIFTRESISTOR_CLOCK 39
#define PIN_TRIAC_SHIFTRESISTOR_LATCH 37
#define PIN_TRIAC_MOTOR_UP 47
#define PIN_TRIAC_MOTOR_DOWN 45

// triac variable setting constant
#define TRIAC_COUNT 18
#define TRIAC_MAX_AMOUNT 10
#define TRIAC_SHIFTRESISTOR_BITORDER LSBFIRST

// heatmode constant
#define HEATMODE_MANUAL 0
#define HEATMODE_AUTO 1
#define HEATMODE_AUTO_MARGINTEMP 0

// tempsensor variable setting constant
#define TEMPSENSOR_DECODER_PINCOUNT 5
#define TEMPSENSOR_COUNT 18

// serial communication synchronize semaphore
SemaphoreHandle_t semSerialLock;

// tempsensor and heat channel variable structure
typedef struct _TemperagtureChannel
{
    float Temperature;
    float Max, Min, Magnitude;
} TemperatureChannel;

typedef struct _HeaterChannel
{
    byte HeaterMode; // 0 = manual, 1 = auto
    byte HeaterAmount;
    float TargetTemperature;
} HeaterChannel;

// tempsensor communication setting variable
byte tempSensorDecoderPin[TEMPSENSOR_DECODER_PINCOUNT] = {33, 31, 29, 27, 25};
byte tempSensorDecoderAddress[TEMPSENSOR_COUNT] = {0, 1, 2, 3, 4, 5, 6, 7, 8, 9, 10, 11, 12, 13, 14, 15, 16, 17};
SPISettings tempSensorSPISetting = SPISettings(4000000, MSBFIRST, SPI_MODE0);
// triac contorol setting variable
byte triacEnablePin[TRIAC_COUNT] = {28, 29, 30, 31, 32, 33};
// channel data array
TemperatureChannel TempChannel[TEMPSENSOR_COUNT];
HeaterChannel HeatChannel[TRIAC_COUNT];
/* 
- TEMP LABEL TO HEAT LABEL 
1 = 11 >> 9 = 19 >> 11 = 1 >> 19 = 9
- TEMP INDEX TO HEAT INDEX
 0 = 9 >> 8 = 17 >> 9 = 0 >> 17 = 8
*/
// tempsensor index and heat index matching table
byte tempChannelToHeatChannel[TEMPSENSOR_COUNT] = {9, 10, 11, 12, 13, 14, 15, 16, 17, 0, 1, 2, 3, 4, 5, 6, 7, 8};
// motor control state variable
int motorOutput = 0;

// task declaration
void tskControlTriac(void *pvParamepters);
void tskReadTemperature(void *pvParameters);
void tskReadSerial(void *pvParameters);
void setTriacSelection(uint32_t selection);
void tskPrintStatus(void *pvParameters);
void tskControlMotor(void *pvParameters);

// setup function
void setup()
{
    /* Serial and IO pin initialize */
    Serial.begin(115200);
    Serial.println("INIT,START");

    pinMode(PIN_TEMPSENSOR_DECODER_ENABLE, OUTPUT);
    pinMode(PIN_TRIAC_SHIFTRESISTOR_DATA, OUTPUT);
    pinMode(PIN_TRIAC_SHIFTRESISTOR_CLOCK, OUTPUT);
    pinMode(PIN_TRIAC_SHIFTRESISTOR_LATCH, OUTPUT);
    pinMode(PIN_TRIAC_MOTOR_UP, OUTPUT);
    pinMode(PIN_TRIAC_MOTOR_DOWN, OUTPUT);

    for (int i = 0; i < TEMPSENSOR_DECODER_PINCOUNT; i++)
    {
        pinMode(tempSensorDecoderPin[i], OUTPUT);
    }

    for (int i = 0; i < TRIAC_COUNT; i++)
    {
        pinMode(triacEnablePin[i], OUTPUT);
        TempChannel[i].Max = -999.9;
        TempChannel[i].Min = 999.9;
        TempChannel[i].Temperature = 0.0;
        HeatChannel[i].HeaterMode = HEATMODE_MANUAL;
        HeatChannel[i].HeaterAmount = 0;
        HeatChannel[i].TargetTemperature = 0;
    }

    semSerialLock = xSemaphoreCreateBinary();
    if (semSerialLock == NULL)
    {
        Serial.println("ERROR,SERIAL_SEMAPHORE_INIT");
        return;
    }
    xSemaphoreGive(semSerialLock);
    Serial.println("INIT,SEMOK");

    /* Begin SPI for temperature sensor*/
    SPI.begin();
    Serial.println("INIT,COMMOK");

    /* Create task and Start scheduler */
    xTaskCreate(tskControlTriac, "ControlTriac", 300, NULL, 3, NULL);
    xTaskCreate(tskReadTemperature, "ReadTemperature", 300, NULL, 3, NULL);
    xTaskCreate(tskPrintStatus, "PrintStatus", 800, NULL, 4, NULL);
    xTaskCreate(tskReadSerial, "ReadSerial", 300, NULL, 2, NULL);
    xTaskCreate(tskControlMotor, "ControlMotor", 300, NULL, 3, NULL);

    Serial.println("STARTSCHEDULER");
    vTaskStartScheduler();
    Serial.println("ERROR,SCHEDULER_FAIL");
}

// loop function isn't used
void loop()
{
}

// triac control task
void tskControlTriac(void *pvParameters)
{
    while (1)
    {
        for (int c = 0; c < TRIAC_MAX_AMOUNT; c++)
        {
            uint32_t curout = 0;
            for (int i = 0; i < TRIAC_COUNT; i++)
            {
                // 0 is on , 1 is off
                curout |= ((HeatChannel[i].HeaterAmount > c ) ? 0 : 1) << i;
            }
            setTriacSelection(curout);
            vTaskDelay((1000 / TRIAC_MAX_AMOUNT) / portTICK_PERIOD_MS);
        }
    }
}

// read tempsensor
void tskReadTemperature(void *pvParameters)
{
    uint8_t resph, respl;
    uint16_t resp;
    byte hi;
    while (1)
    {
        for (int i = 0; i < TEMPSENSOR_COUNT; i++)
        {
            // retieve data through spi communication
            SPI.beginTransaction(tempSensorSPISetting);
            digitalWrite(PIN_TEMPSENSOR_DECODER_ENABLE, LOW);
            setTempSensorDecoder(tempSensorDecoderAddress[i]);
            resph = SPI.transfer(0x00, SPI_CONTINUE);
            respl = SPI.transfer(0x00);
            SPI.endTransaction();
            digitalWrite(PIN_TEMPSENSOR_DECODER_ENABLE, HIGH);

            // assign data to channel
            resp = (resph << 8) | respl;
            TempChannel[i].Temperature = ((resp & 0x7FF8) >> 3) * 0.25;
            if (TempChannel[i].Max <= TempChannel[i].Temperature)
                TempChannel[i].Max = TempChannel[i].Temperature;
            if (TempChannel[i].Min >= TempChannel[i].Temperature)
                TempChannel[i].Min = TempChannel[i].Temperature;
            
            // set heat level from temp channel
            hi = tempChannelToHeatChannel[i];
            if (HeatChannel[hi].HeaterMode == HEATMODE_AUTO) {
                if (HeatChannel[hi].TargetTemperature - TempChannel[i].Temperature  > HEATMODE_AUTO_MARGINTEMP) {
                    HeatChannel[hi].HeaterAmount = 10;
                } else {
                    HeatChannel[hi].HeaterAmount = 0;
                }
            }
        }
        vTaskDelay(1000 / portTICK_PERIOD_MS);
    }
}

// serial read task
void tskReadSerial(void *pvParameters)
{
    Serial.setTimeout(1000);
    char buf[10];
    while (1)
    {
        if (Serial.available())
        {
            if (Serial.readBytesUntil(255, buf, 10) > 2)
            {
                switch (buf[0])
                {
                case 1: // HEATER
                    HeatChannel[buf[1]].HeaterAmount = buf[2];
                    SerialPrintlnSync("OK,HEATER");
                    break;
                case 2: // HEATER RANGE
                    for (int i = buf[1]; i <= buf[2]; i++) {
                        HeatChannel[i].HeaterAmount = buf[3];
                    }
                    SerialPrintlnSync("OK,HEATERRANGE");
                    break;
                case 3: // MOTOR
                    motorOutput = buf[1] - 128;
                    SerialPrintlnSync("OK,MOTOR");
                    break;
                case 4: // MODE
                    HeatChannel[buf[1]].HeaterMode = buf[2];
                    SerialPrintlnSync("OK,MODE");
                    break;
                case 5: // MODE RANGE
                    for (int i = buf[1]; i <= buf[2]; i++) {
                        HeatChannel[i].HeaterMode = buf[3];
                    }
                    SerialPrintlnSync("OK,MODERANGE");
                    break;
                case 6: // TARGET TEMP
                    HeatChannel[buf[1]].TargetTemperature = buf[2] + buf[3]*256.0f;
                    SerialPrintlnSync("OK,TARGETTEMP");
                    break;
                case 7: // TARGET TEMP RANGE
                    for (int i = buf[1]; i <= buf[2]; i++) {
                        HeatChannel[i].TargetTemperature = buf[3] + buf[4]*256.0f;
                    }
                    SerialPrintlnSync("OK,TARGETTEMPRANGE");
                    break;
                }
            }
        }
    }
}

// motor control task
void tskControlMotor(void *pvParameters) {
    while (1) {
        if (motorOutput > 0) { //UP
            digitalWrite(PIN_TRIAC_MOTOR_UP, HIGH);
            digitalWrite(PIN_TRIAC_MOTOR_DOWN, LOW);
            SerialPrintlnSync("OK,MOTORUP");
            motorOutput--;
        } else if (motorOutput == 0) { //NEUTRAL
            digitalWrite(PIN_TRIAC_MOTOR_UP, LOW);
            digitalWrite(PIN_TRIAC_MOTOR_DOWN, LOW);
        } else { //DOWN
            digitalWrite(PIN_TRIAC_MOTOR_UP, LOW);
            digitalWrite(PIN_TRIAC_MOTOR_DOWN, HIGH);
            SerialPrintlnSync("OK,MOTORDOWN");
            motorOutput++;
        }
        vTaskDelay(100 / portTICK_PERIOD_MS);
    }
}

// status print task
void tskPrintStatus(void *pvParameters)
{
    char sentence[250], buffer[10];
    while (1)
    {
        strcpy(sentence, "TEMP");
        for (int i = 0; i < TEMPSENSOR_COUNT; i++)
        {
            sprintf(buffer, ",%.2f", TempChannel[i].Temperature);
            strcat(sentence, buffer);
        }
        SerialPrintlnSync(sentence);

        strcpy(sentence, "OUT");
        for (int i = 0; i < TRIAC_COUNT; i++)
        {
            sprintf(buffer, ",%d", HeatChannel[i].HeaterAmount);
            strcat(sentence, buffer);
        }
        SerialPrintlnSync(sentence);

        strcpy(sentence, "MODE");
        for (int i = 0; i < TRIAC_COUNT; i++)
        {
            sprintf(buffer, ",%d", HeatChannel[i].HeaterMode);
            strcat(sentence, buffer);
        }
        SerialPrintlnSync(sentence);

        strcpy(sentence, "TARGETTEMP");
        for (int i = 0; i < TRIAC_COUNT; i++)
        {
            sprintf(buffer, ",%.2f", HeatChannel[i].TargetTemperature);
            strcat(sentence, buffer);
        }
        SerialPrintlnSync(sentence);
        vTaskDelay(1500 / portTICK_PERIOD_MS);
    }
}

// traic shift-register select function
void setTriacSelection(uint32_t selection)
{
    digitalWrite(PIN_TRIAC_SHIFTRESISTOR_LATCH, LOW);
    selection = selection << 6;
    shiftOut(PIN_TRIAC_SHIFTRESISTOR_DATA, PIN_TRIAC_SHIFTRESISTOR_CLOCK, TRIAC_SHIFTRESISTOR_BITORDER, selection);
    shiftOut(PIN_TRIAC_SHIFTRESISTOR_DATA, PIN_TRIAC_SHIFTRESISTOR_CLOCK, TRIAC_SHIFTRESISTOR_BITORDER, selection >> 8);
    shiftOut(PIN_TRIAC_SHIFTRESISTOR_DATA, PIN_TRIAC_SHIFTRESISTOR_CLOCK, TRIAC_SHIFTRESISTOR_BITORDER, selection >> 16);
    digitalWrite(PIN_TRIAC_SHIFTRESISTOR_LATCH, HIGH);
}

// heat buffer select function
void setTempSensorDecoder(byte selection)
{
    uint32_t output;
    for (int i = 0; i < TEMPSENSOR_DECODER_PINCOUNT; i++)
    {
        if ((selection & (1 << i)) > 0)
        {
            output = HIGH;
        }
        else
        {
            output = LOW;
        }
        digitalWrite(tempSensorDecoderPin[i], output);
    }
}

// serial print function
int SerialPrintlnSync(char *str)
{
    if (xSemaphoreTake(semSerialLock, (TickType_t)1000 / portTICK_PERIOD_MS) == pdTRUE)
    {
        Serial.println(str);
        xSemaphoreGive(semSerialLock);
        return 0;
    }
    else
    {
        return -1;
    }
}
